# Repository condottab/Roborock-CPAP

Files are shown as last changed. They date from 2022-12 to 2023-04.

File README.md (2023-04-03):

# Roborock-CPAP
Remote blowing system using a Roborock fan


This repo contains all the data I have collected about wiring, controlling and powering the Roborock fan. If a connection and control method is not mentioned here, it is considered unsafe or has not been tested. As always, everything you do is at your own risk.

There are several types of these fans on the market from different manufacturers, qinatsu and nidec have been tested. At the moment only one type of fan is considered unsuitable for our purposes, the 5 pin 5.1kPA (or 5100) option from nidec, the others have been found to work. Chinese sellers often give them in terms of nominal pressure capacity, which probably has nothing to do with actual performance, but we can try to work out what to buy and what not to buy from these values. It has been found that the 2.5kPa option often means a Qinatsu fan, which heats less than a Nidec, but they both work fine. I also noticed that the high-pitched pwm noise was worse with the Qinatsu. If you're not using active fan cooling, it's a good idea to set the maximum fan speed to around 0.6-0.7 in the config. It will still provide plenty of airflow.

The connection is as follows:

PWM > HARDWARE PWM pin on the mainboard

VCC > 24V hotend output from the mainboard

GND > Grounded pin of the hotend output prescribed as enable_pin: PIN in the fan config

FG > Doesn't go anywhere yet, but you can tinker with it if you know what you're doing.

To get started, you will need to make a small flyback protection board, which includes a 10k resistor to pull down the fan's PWM pin.





You can also order this board to be produced for you, there is a gerber file for this.




Many thanks to [stas2z](https://github.com/stas2z) for his expertise and work in researching various fans, putting together the protection schematics and providing the gerber. You are a legend and a guiding star.

BOM 

BZX55C5V1 x2

1N5819 x1 (x4 if you want to use three in parallel instead of one 1N5822)

1N5822 x1

CF2WS-1K x1

CF2WS-10K x1 (+1 if you want to use a grounded pin of the fan output for pwm)

PH 2.0 connector x1

Heat inserts m3x4.2x4 x5

M3x5 screws x5

The printed parts are in abs and tpu.

SMD BOM

MDD DSK24 x1

BZT52C5V1S x2

102 resistor x1

103 resistor x1

SS56F x 1

PH 2.0 connector x1





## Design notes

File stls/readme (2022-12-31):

Everything except the backplate hose connector and inlet grommet can be printed in hard plastic of your choice. The latter two must be printed in tpu.

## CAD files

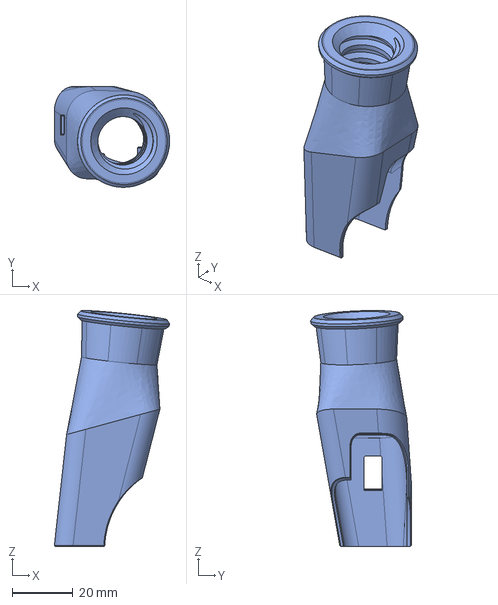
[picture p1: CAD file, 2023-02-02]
cad/fan_to_hose_adapter_18mm.step
37.9 x 33.1 x 77.6 mm

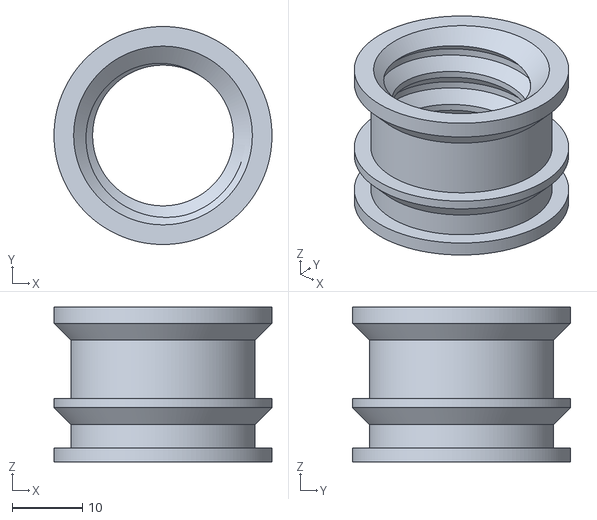
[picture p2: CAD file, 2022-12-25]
stls/bacplate_hose_connector_22mmOD.stl
31.0 x 31.0 x 22.0

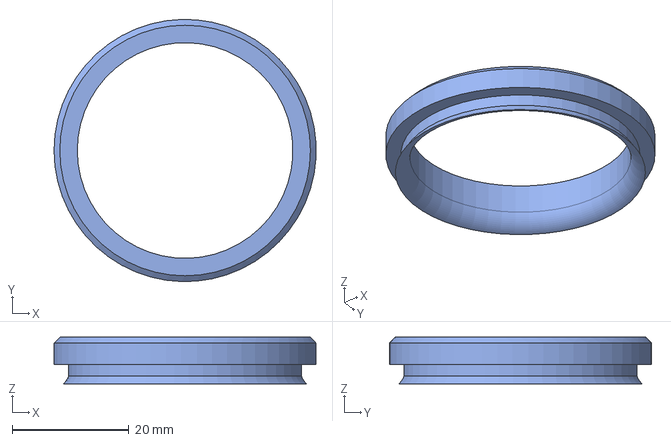
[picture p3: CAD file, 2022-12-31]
cad/inlet_grommet.step
45.0 x 45.0 x 8.00 mm

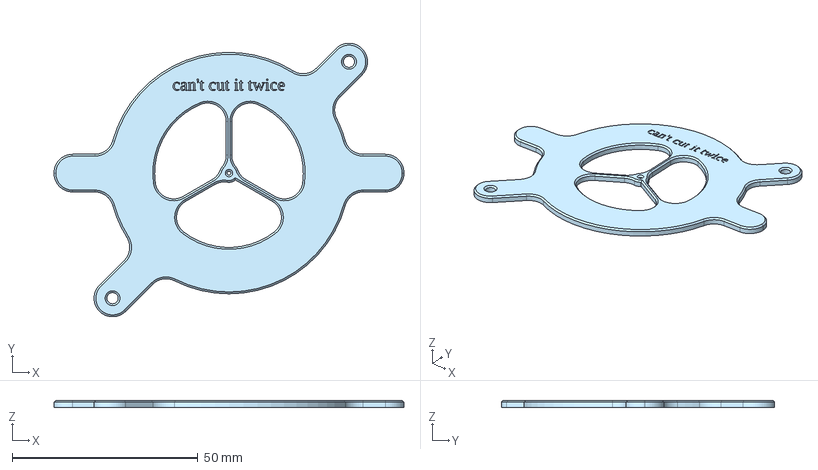
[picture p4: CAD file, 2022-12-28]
cad/drilling_template.step
94.2 x 73.6 x 2.00 mm

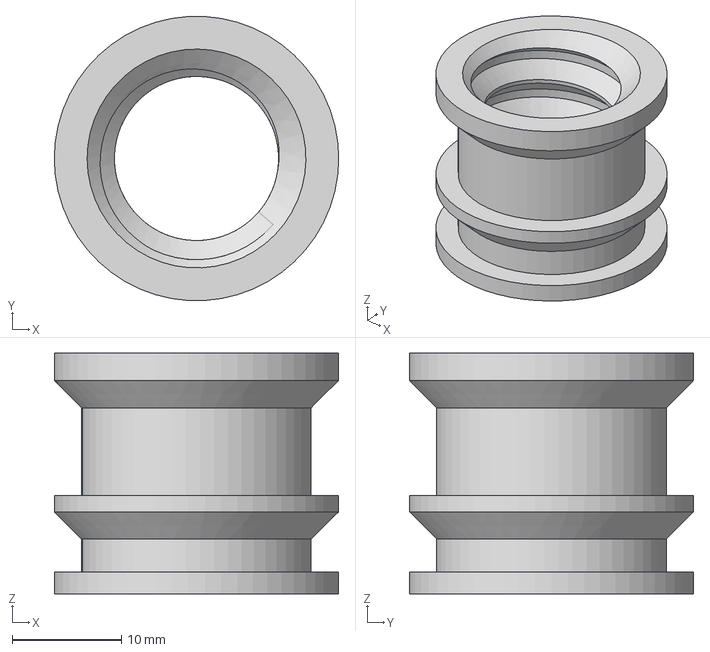
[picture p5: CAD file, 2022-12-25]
cad/backplate_hose_connector_18mmOD.step
26.0 x 26.0 x 22.0 mm

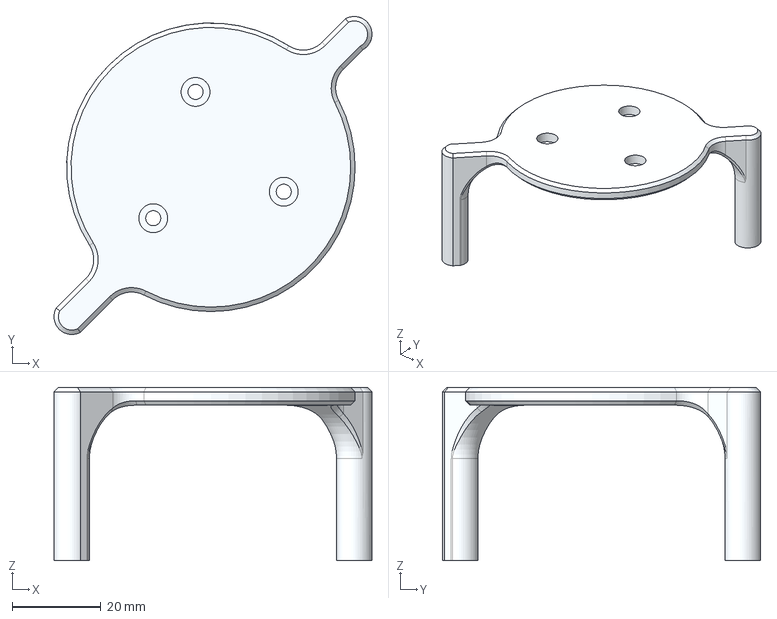
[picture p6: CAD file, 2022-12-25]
cad/mount_plate_no_logo.step
71.6 x 71.6 x 39.0 mm

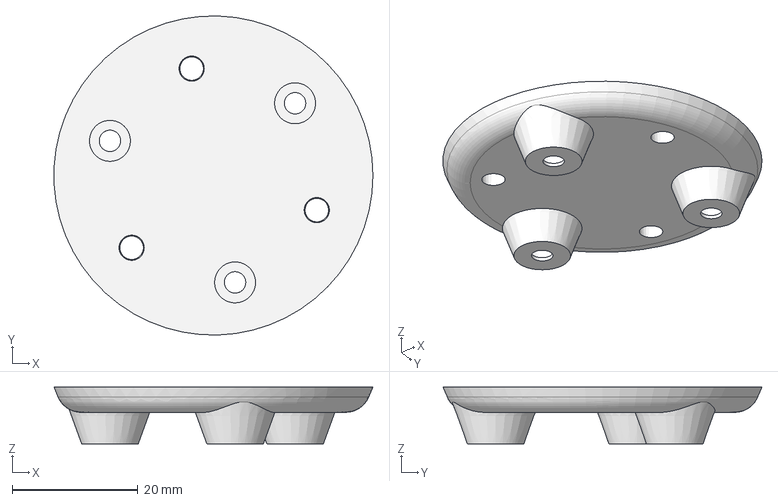
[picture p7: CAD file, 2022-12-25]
cad/adapter_plate.step
50.6 x 50.7 x 9.00 mm

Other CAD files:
cad/fan_to_hose_adapter_22mm.step
cad/fan_to_hose_adapter_18mm_nidec_black.step
cad/fan_to_hose_adapter_22mm_nidec_black.step
cad/backplate_hose_connector_22mmOD.step
cad/mount_plate.step
stls/adapter_plate.stl
stls/backplate_hose_connector_18mmOD.stl
stls/drilling_template.stl
stls/inlet_grommet.stl
stls/mount_plate.stl

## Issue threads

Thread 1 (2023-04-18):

The fan does not start.

pavluchenkor, 2023-04-18:
For the test, I assembled the stm32 stand, the fan and the circuit that you kindly provided. Everything is connected to the power supply, common ground is everywhere, PWM is generated from minimum to maximum and back, the LED is connected in parallel to the fan input, and the PWM operation is clearly visible, i.e. the LED changes brightness, but the fan does not work. While the fan is connected to a power source, nothing happens, but it is only necessary to disconnect and connect the fan power, as it starts to work. I assume you are facing such a problem and that is why I am looking for a solution here. Tell me what can be done?

ripinteer, 2023-04-18:
Looks like Nidec fan you have. They require to be powered from controllable hotend output, so the motherboard can handle the power set routine automatically. Check out the .cfg Nidec example in this repo

pavluchenkor, 2023-04-18:
Thanks for the reply! That's right, it is Nidec, I forgot to report it. I looked at this example, everything is clear there, but I do not understand the nuances.
enable_pin: <hotend_output_grounded_pin> Should it be the hotend pin or any driven pin with high current?

pavluchenkor, 2023-04-18:
And one more question. In case PWM for fan will be 0 klipper will turn off enable_fan_pin pin by itself, and when pwm will be more than 0 on enable_fan_pin there will be high level? Sorry, I'm not at all familiar with the inner workings of klipper and I'm concerned about the usual situation where I don't need fanning during printing for some reason and PWM = 0, but the next moment I need fanning. Do I understand the logic correctly, it is the klipper that controls enable_fan_pin itself based on the PWM value?

pavluchenkor, 2023-07-07:
Please tell me, what should be the voltage of pwm, 5, 12 or 24V?

Closed 2023-04-18.

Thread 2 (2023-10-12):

Want to start the fan without controller just to test it.

Shamoon78, 2023-10-12:
So if I connect the vcc to 12 volt and the ground does the fan work ?in full speed even is ok just to test it.

condottab, 2023-10-20:
To test the fan, you should supply power and PWM simultaneously. Say 5V to the PWM and 12V to the power line.

Closed 2023-10-20.

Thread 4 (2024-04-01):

How it compares to a 120 blower fan?

dbuezas, 2024-04-01:
Would you recommend it over a 120 blower fan?
Also, can the pwm pin be driven at 24v?
I intend to use the existing fan output pin of my board, which is already protected.

Thanks!

condottab, 2024-04-11:
Yes.
No.
Don't.

Closed 2024-04-11.

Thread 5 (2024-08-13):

how to determine pwm out pin for mks boards?

selimayaz, 2024-08-13:
Hello, thanks for useful project. I wonder which pin to use pwm out for MKS-Monster8. Thanks..

condottab, 2024-08-21:
Not familiar with a board. Usually the neopixel/led pin works best because of the 5v pullup. If hw pwm doesn't work, try software pwm, this is a known problem for many boards.

condottab, 2024-08-21:
Not familiar with a board. Usually the neopixel/led pin works best because of the 5v pullup. If hw pwm doesn't work, try software pwm, this is a known problem for many boards.

Closed 2024-08-21.

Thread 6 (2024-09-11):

SMD BOM has extra Schottky diode

ReillyBex, 2024-09-11:
The SMD BOM includes both a MDD DSK24 as well as a SS56F but only the DSK24 is called out on the PCB.

ReillyBex, 2024-09-11:
nvm I'm a dumbass lol.

Closed 2024-09-11.

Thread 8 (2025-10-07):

Using the Roborock CPAP in klipper always needs a power cycle to work

ddvxx, 2025-10-07:
Once I put some fan speed, i have to disconnect the cpap from the 24v to work, does anyones know how to fix It or if i just have to config something on klipper?
